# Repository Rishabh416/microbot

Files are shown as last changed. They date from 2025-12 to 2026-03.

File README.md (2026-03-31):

# Microbot

My first fully custom project inspired by the microbots from the movie Big Hero 6. My goal is to get into swarm robotics and I believe this is a HUGE leap in that direction, but a good moment to learn. I made this project to learn about swarm robotics and the potential application in environmental applications such as in deserts. 

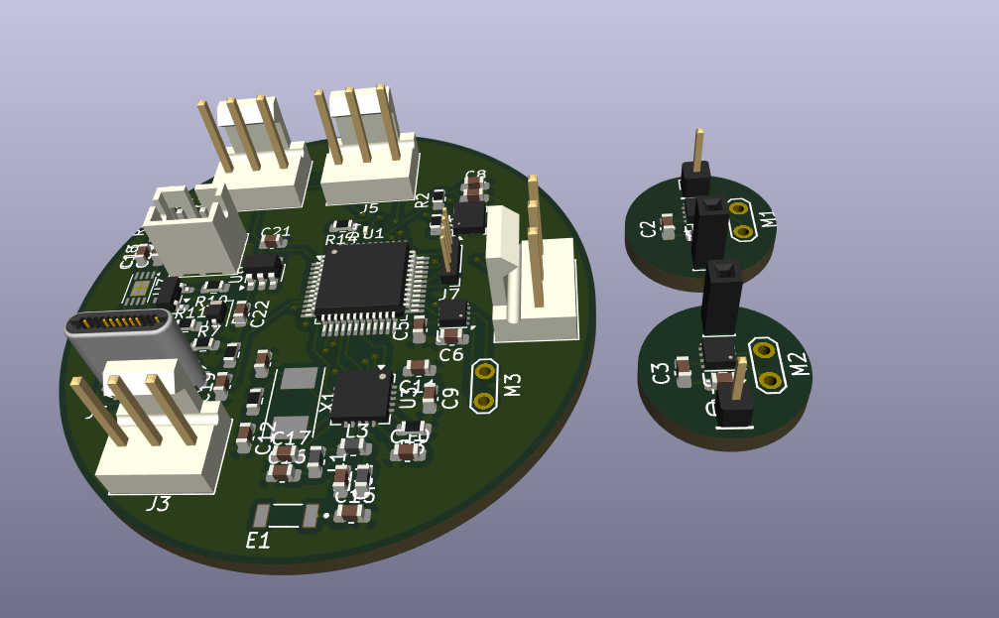
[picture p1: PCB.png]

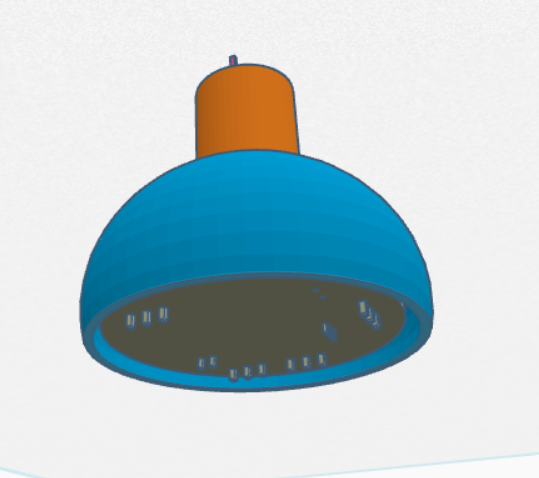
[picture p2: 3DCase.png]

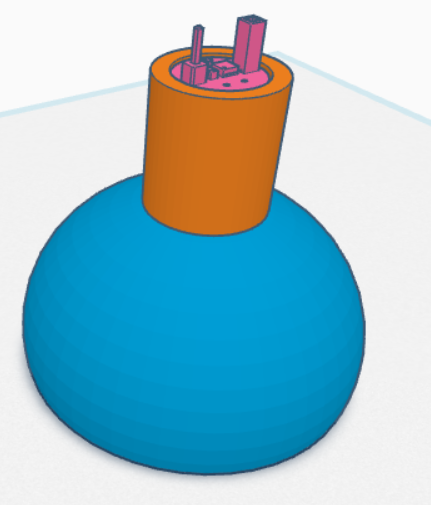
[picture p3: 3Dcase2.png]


| Part Number | JLC Part Number | Description | Manufacturer | Package | URL |
| :--- | :--- | :--- | :--- | :--- | :--- |
| STM32F103C8T6 | C8734 | STM32 MCU | STMicroelectronics | LQFP-48(7x7) | [Link](https://jlcpcb.com/partdetail/STMicroelectronics-STM32F103C8T6/C8734) |
| N/A | N/A | Electromagnet | | | |
| | N/A | Servo Motor | | | |
| | N/A | DC Motor | | | |
| ICM-42688-P(TOKMAS) | C54308212 | IMU | Tokmas | LGA-14(2.5x3) | [Link](https://jlcpcb.com/partdetail/Tokmas-ICM_42688_P_TOKMAS/C54308212) |
| NRF24L01P-R | C8791 | NRF24 | Nordic Semicon | QFN-20-EP(4x4) | [Link](https://jlcpcb.com/partdetail/NordicSemicon-NRF24L01PR/C8791) |
| KH-204065-DZ | C530676 | Pogo Male | Shenzhen Kinghelm Elec | SMD, D=2mm | [Link](https://jlcpcb.com/partdetail/Shenzhen_KinghelmElec-KH_204065DZ/C530676) |
| BWCD-L4.5W2.0H2.3 | C2826546 | Pogo Female | BAT WIRELESS | SMD, D=2mm | [Link](https://jlcpcb.com/partdetail/BATWIRELESS-BWCD_L4_5W2_0H23/C2826546) |
| | N/A | LiPo Battery | | | |
| MCP73831-2ATI/MC | C635036 | BMS | Microchip Tech | DFN-8-EP(2x3) | [Link](https://jlcpcb.com/partdetail/MicrochipTech-MCP73831_2ATIMC/C635036) |
| XC6220B331MR-G | C86534 | Voltage Regulator | Torex Semicon | SOT-25 | [Link](https://jlcpcb.com/partdetail/TorexSemicon-XC6220B331MRG/C86534) |
| DRV8837CDSGR | C191000 | Motor Driver | Texas Instruments | WSON-8-EP(2x2) | [Link](https://jlcpcb.com/partdetail/TexasInstruments-DRV8837CDSGR/C191000) |
| 2450AT18A100E | C89334 | Antenna | Johanson Dielectrics | 1206 | [Link](https://jlcpcb.com/partdetail/JohansonDielectrics-2450AT18A100E/C89334) |
| 16M 12PF 10PPM | C2975359 | 16MHz Crystal | SST | HC-49S-SMD-2P-Mini | [Link](https://jlcpcb.com/partdetail/SST-16M_12PF10PPM/C2975359) |
| SSM3J338R,LF | C146352 | MOSFET | TOSHIBA | SOT-23F | [Link](https://jlcpcb.com/partdetail/TOSHIBA-SSM3J338RLF/C146352) |
| | | Capacitors | | 0603 | |
| HVRTB-3433EPX | C5246356 | Green LED | HONGLITRONIC | SMD-6P, 3.4x3.3mm | [Link](https://jlcpcb.com/partdetail/5956669-HVRTB3433EPX/C5246356) |
| | | Diodes | | D_SOD-323 | |
| TJ-S0704EX4T5ALC2R-A5 | C48689442 | Red LED | TOGIALED | 0201 | [Link](https://jlcpcb.com/partdetail/TOGIALED-TJ_S0704EX4T5ALC2RA5/C48689442) |
| 918-118A2021Y40002 | C399939 | USB C | Jing Extension | SMD | [Link](https://jlcpcb.com/partdetail/383027-918118A2021Y40002/C399939) |
| B2B-PH-K-S-GW | C5251182 | Conn_01x02 | JST | 插件, P=2mm | [Link](https://jlcpcb.com/partdetail/JST-B2B_PH_K_SGW/C5251182) |
| 2.54-1*3P针 | C49257 | Conn_01x03_Pin | BOOMELE | 插件, P=2.54mm | [Link](https://jlcpcb.com/partdetail/50265-2_54_1_3P/C49257) |
| 2.54-1*4 | C5116483 | Conn_01x04_Pin | ZHOURI | 插件, P=2.54mm | [Link](https://jlcpcb.com/partdetail/ZHOURI-2_54_14/C5116483) |
| | | Inductors | | 0603 | |
| | | Resistors | | 0603 | |

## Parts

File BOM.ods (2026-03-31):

Part Number | JLC Part Number | Description | Manufacturer | Package | URL
STM32F103C8T6 | C8734 | STM32 MCU | STMicroelectronics | LQFP-48(7x7) | https://jlcpcb.com/partdetail/STMicroelectronics-STM32F103C8T6/C8734
N/A | N/A | Electromagnet
 | N/A | Servo Motor
 | N/A | DC Motor
ICM-42688-P(TOKMAS) | C54308212 | IMU | Tokmas | LGA-14(2.5x3) | https://jlcpcb.com/partdetail/Tokmas-ICM_42688_P_TOKMAS/C54308212
NRF24L01P-R | C8791 | NRF24 | Nordic Semicon | QFN-20-EP(4x4) | https://jlcpcb.com/partdetail/NordicSemicon-NRF24L01PR/C8791
KH-204065-DZ | C530676 | Pogo Male | Shenzhen Kinghelm Elec | SMD,D=2mm | https://jlcpcb.com/partdetail/Shenzhen_KinghelmElec-KH_204065DZ/C530676
BWCD-L4.5W2.0H2.3 | C2826546 | Pogo Female | BAT WIRELESS | SMD,D=2mm | https://jlcpcb.com/partdetail/BATWIRELESS-BWCD_L4_5W2_0H23/C2826546
 | N/A | LiPo Battery
MCP73831-2ATI/MC | C635036 | BMS | Microchip Tech | DFN-8-EP(2x3) | https://jlcpcb.com/partdetail/MicrochipTech-MCP73831_2ATIMC/C635036
XC6220B331MR-G | C86534 | Voltage Regulator | Torex Semicon | SOT-25 | https://jlcpcb.com/partdetail/TorexSemicon-XC6220B331MRG/C86534
DRV8837CDSGR | C191000 | Motor Driver | Texas Instruments | WSON-8-EP(2x2) | https://jlcpcb.com/partdetail/TexasInstruments-DRV8837CDSGR/C191000
2450AT18A100E | C89334 | Antenna | Johanson Dielectrics | 1206 | https://jlcpcb.com/partdetail/JohansonDielectrics-2450AT18A100E/C89334
16M 12PF 10PPM | C2975359 | 16MHz Crystal | SST | HC-49S-SMD-2P-Mini | https://jlcpcb.com/partdetail/SST-16M_12PF10PPM/C2975359
SSM3J338R,LF | C146352 | MOSFET | TOSHIBA | SOT-23F | https://jlcpcb.com/partdetail/TOSHIBA-SSM3J338RLF/C146352
 |  | Capacitors |  | 0603
HVRTB-3433EPX | C5246356 | Green LED | HONGLITRONIC(Hongli Zhihui (HONGLITRONIC)) | SMD-6P,3.4x3.3mm | https://jlcpcb.com/partdetail/5956669-HVRTB3433EPX/C5246356
 |  | Diodes |  | D_SOD-323
TJ-S0704EX4T5ALC2R-A5 | C48689442 | Red LED | TOGIALED | 0201 | https://jlcpcb.com/partdetail/TOGIALED-TJ_S0704EX4T5ALC2RA5/C48689442
918-118A2021Y40002 | C399939 | USB C | Jing Extension of the Electronic Co. | SMD | https://jlcpcb.com/partdetail/383027-918118A2021Y40002/C399939
B2B-PH-K-S-GW | C5251182 | Conn_01x02 | JST | 插件,P=2mm | https://jlcpcb.com/partdetail/JST-B2B_PH_K_SGW/C5251182
2.54-1*3P针 | C49257 | Conn_01x03_Pin | BOOMELE(Boom Precision Elec) | 插件,P=2.54mm | https://jlcpcb.com/partdetail/50265-2_54_1_3P/C49257
2.54-1*4 | C5116483 | Conn_01x04_Pin | ZHOURI | 插件,P=2.54mm | https://jlcpcb.com/partdetail/ZHOURI-2_54_14/C5116483
 |  | Inductors |  | 0603
 |  | Resistors |  | 0603

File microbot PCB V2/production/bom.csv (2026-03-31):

Designator | Footprint | Quantity | Value | LCSC Part #
C1, C2, C3, C4, C5, C6, C7, C8 | 0603 | 8 | 100n
C10, C19 | 0603 | 2 | 1n
C11 | 0603 | 1 | 33n
C12, C13 | 0603 | 2 | 22p
C14 | 0603 | 1 | 1.5p
C15 | 0603 | 1 | 1p
C16 | 0603 | 1 | 2.2n
C17 | 0603 | 1 | 4.7p
C18, C21 | 0603 | 2 | 10u
C20 | 0603 | 1 | 4.7u
C22 | 0603 | 1 | 1u
C9 | 0603 | 1 | 10n
D1 | 0201 | 1 | Green
D2, D3 | D_SOD-323 | 2 | 1N5819WS
D4 | 0201 | 1 | Red
E1 | XCVR_2450AT18A0100001E | 1 | 2450AT18A0100001E
J1 | USB_C_Plug_ShenzhenJingTuoJin_918-118A2021Y40002_Vertical | 1 | USB_C_Receptacle_PowerOnly_6P
J2 | JST_PH_B2B-PH-K_1x02_P2.00mm_Vertical | 1 | Conn_01x02
J3, J4, J5, J6 | FanPinHeader_1x03_P2.54mm_Vertical | 4 | Conn_01x03_Pin
J7 | PinHeader_1x04_P1.00mm_Vertical | 1 | Conn_01x04_Pin
L1 | 0603 | 1 | 2.7n
L2 | 0603 | 1 | 3.9n
L3 | 0603 | 1 | 8.2n
M1, M2, M3 | TestPoint_2Pads_Pitch2.54mm_Drill0.8mm | 3 | Motor_DC
Q1 | SOT-23 | 1 | Si2371EDS
R1, R10, R11, R2, R5, R6 | 0603 | 6 | 10k
R12 | 0603 | 1 | 75k
R13 | 0603 | 1 | 100k
R14 | 0603 | 1 | 150
R3 | 0603 | 1 | 22k
R4, R9 | 0603 | 2 | 1M
R7, R8 | 0603 | 2 | 5.1k
TP1, TP3 | PinHeader_1x01_P2.00mm_Vertical | 2 | MalePogo
TP2, TP4 | PinSocket_1x01_P2.00mm_Vertical | 2 | FemalePogo
U1 | LQFP-48_7x7mm_P0.5mm | 1 | STM32F103C8Tx
U2 | LGA-14_3x2.5mm_P0.5mm_LayoutBorder3x4y | 1 | LSM6DS3
U3 | QFN-20-1EP_4x4mm_P0.5mm_EP2.5x2.5mm | 1 | nRF24L01P
U4, U5, U6 | WSON-8-1EP_2x2mm_P0.5mm_EP0.9x1.6mm | 3 | DRV8837C
U7 | DFN-8-1EP_3x2mm_P0.5mm_EP1.7x1.4mm | 1 | MCP73831-2-MC
U8 | SOT-23-5 | 1 | XC6220B331MR
X1 | Crystal_SMD_Abracon_ABM7-2Pin_6.0x3.5mm | 1 | 16MHz

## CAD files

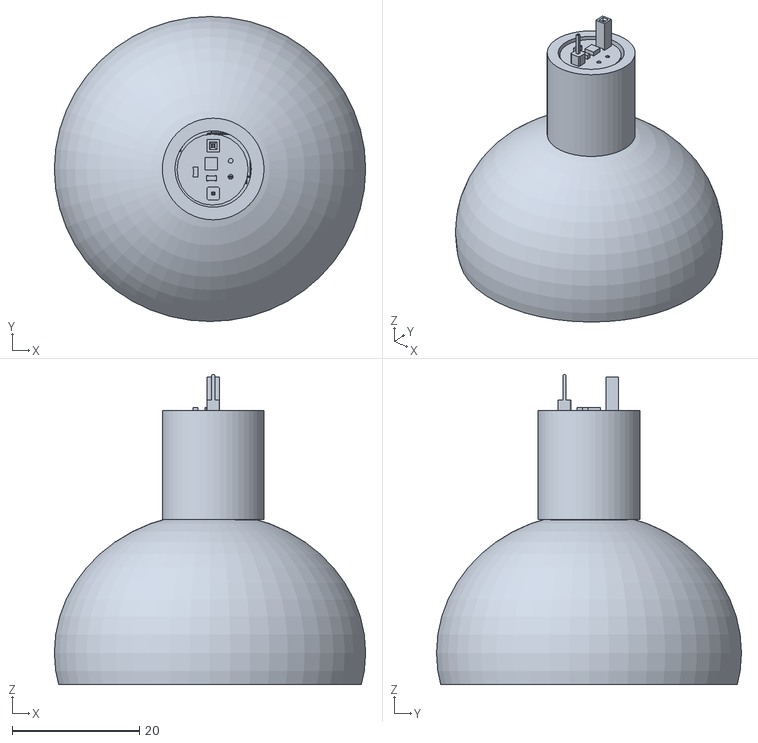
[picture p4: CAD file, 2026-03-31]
Microbot Case V2.stl
49.0 x 48.0 x 48.8

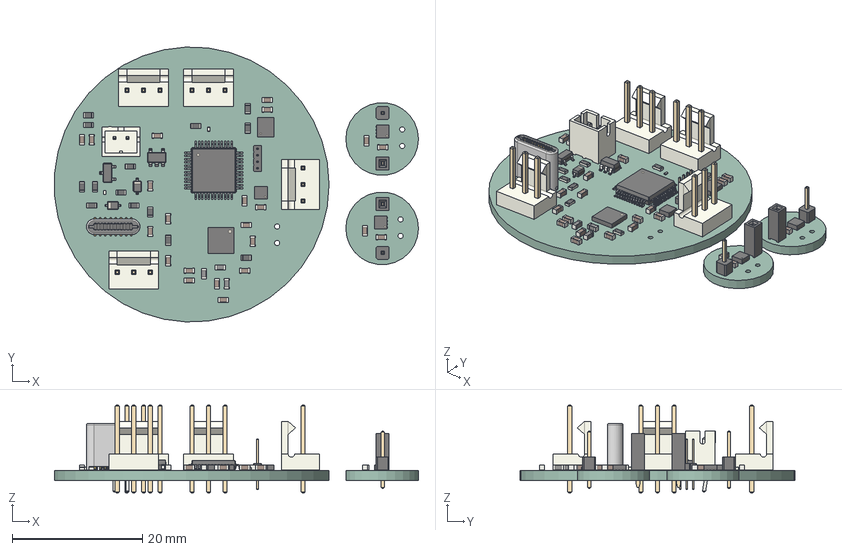
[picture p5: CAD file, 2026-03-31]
microbot PCB V2/MicroBot.step
56.0 x 42.3 x 13.5 mm
JST_PH_B2B-PH-K_1x02_P2.00mm_Vertical
C_0603_1608Metric x 22
R_0603_1608Metric x 14
USB_C_Plug_ShenzhenJingTuoJin_918-118A2021Y40002_Vertical
D_SOD-323 x 2
PinSocket_1x01_P2.00mm_Vertical x 2
PinHeader_1x01_P2.00mm_Vertical x 2
LED_0201_0603Metric x 2
L_0603_1608Metric x 3
SOT-23-5
FanPinHeader_1x03_P2.54mm_Vertical x 4
QFN-20-1EP_4x4mm_P0.5mm_EP2.5x2.5mm
WSON-8-1EP_2x2mm_P0.5mm_EP0.9x1.6mm x 3
LQFP-48_7x7mm_P0.5mm
LGA-14_3x2.5mm_P0.5mm_LayoutBorder3x4y
SOT-23
PinHeader_1x04_P1.00mm_Vertical
MicroBot_PCB_1
MicroBot_PCB_2
MicroBot_PCB_3

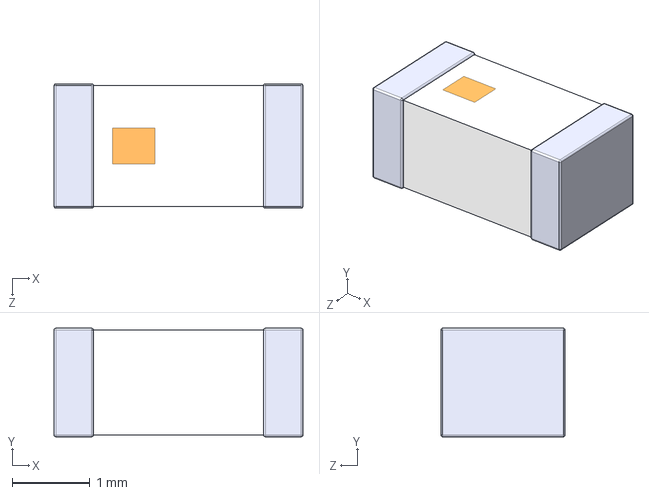
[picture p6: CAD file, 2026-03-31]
microbot PCB V2/SymbolFootprint/2450AT18A0100001E/2450AT18A0100001E.step
3.20 x 1.40 x 1.60 mm

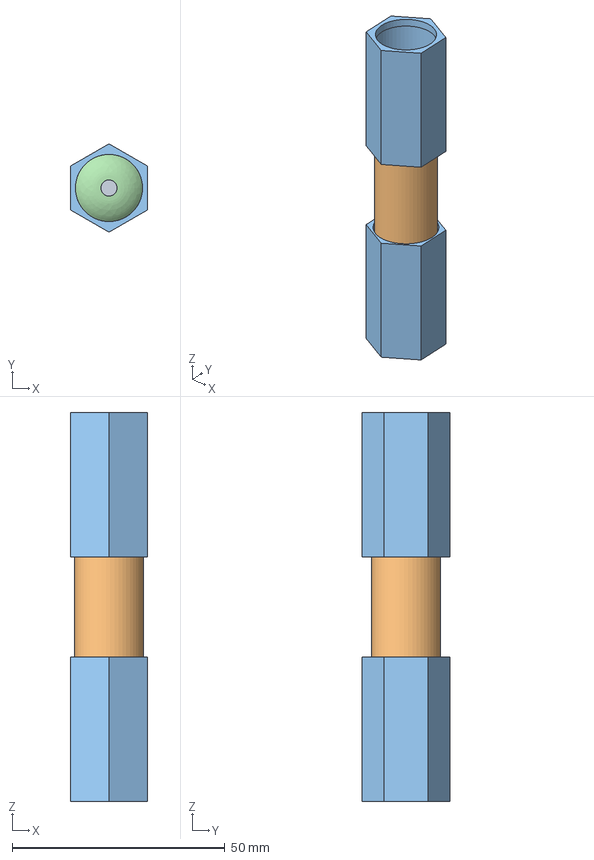
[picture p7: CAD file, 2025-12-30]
Microbot Case.step
18.0 x 20.8 x 91.5 mm
PCB
Central Case
Arm

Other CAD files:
Microbot Case.f3d
Microbot.f3d

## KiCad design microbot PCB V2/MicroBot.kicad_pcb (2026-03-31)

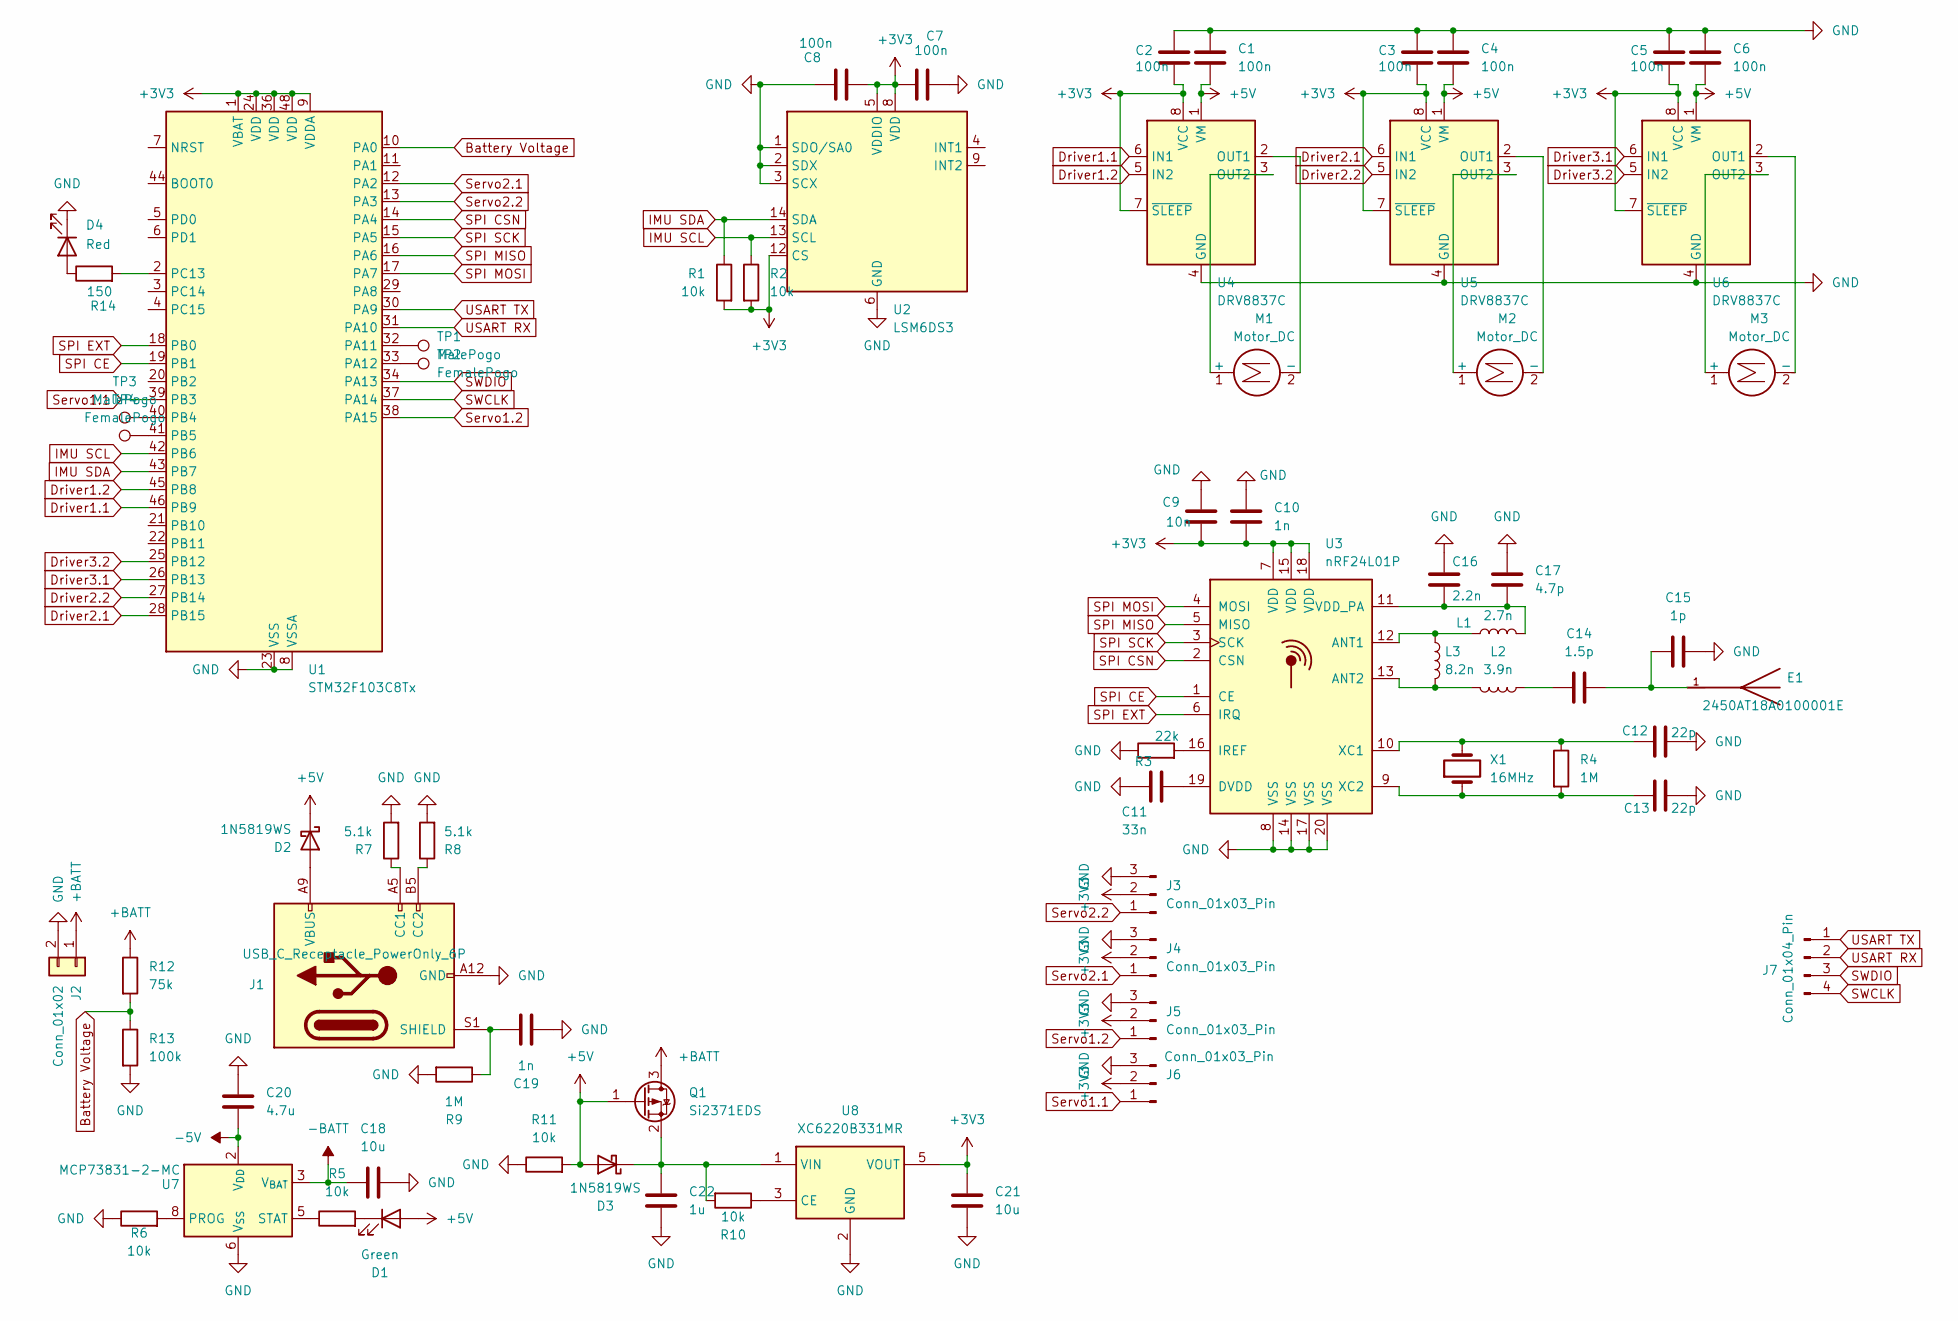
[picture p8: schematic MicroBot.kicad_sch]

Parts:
C1, C2, C3, C4, C5, C6, C7, C8: 100n; C_0603_1608Metric
C9: 10n; C_0603_1608Metric
C10, C19: 1n; C_0603_1608Metric
C11: 33n; C_0603_1608Metric
C12, C13: 22p; C_0603_1608Metric
C14: 1.5p; C_0603_1608Metric
C15: 1p; C_0603_1608Metric
C16: 2.2n; C_0603_1608Metric
C17: 4.7p; C_0603_1608Metric
C18, C21: 10u; C_0603_1608Metric
C20: 4.7u; C_0603_1608Metric
C22: 1u; C_0603_1608Metric
D1: Green; LED_0201_0603Metric
D2, D3: 1N5819WS; D_SOD-323
D4: Red; LED_0201_0603Metric
E1: 2450AT18A0100001E; XCVR_2450AT18A0100001E; PARTREV 4.0
J1: USB_C_Receptacle_PowerOnly_6P; USB_C_Plug_ShenzhenJingTuoJin_918-118A2021Y40002_Vertical
J2: Conn_01x02; JST_PH_B2B-PH-K_1x02_P2.00mm_Vertical
J3, J4, J5, J6: Conn_01x03_Pin; FanPinHeader_1x03_P2.54mm_Vertical
J7: Conn_01x04_Pin; PinHeader_1x04_P1.00mm_Vertical
L1: 2.7n; L_0603_1608Metric
L2: 3.9n; L_0603_1608Metric
L3: 8.2n; L_0603_1608Metric
M1, M2, M3: Motor_DC; TestPoint_2Pads_Pitch2.54mm_Drill0.8mm
Q1: Si2371EDS; SOT-23
R1, R2, R5, R6, R10, R11: 10k; R_0603_1608Metric
R3: 22k; R_0603_1608Metric
R4, R9: 1M; R_0603_1608Metric
R7, R8: 5.1k; R_0603_1608Metric
R12: 75k; R_0603_1608Metric
R13: 100k; R_0603_1608Metric
R14: 150; R_0603_1608Metric
TP1, TP3: MalePogo; PinHeader_1x01_P2.00mm_Vertical
TP2, TP4: FemalePogo; PinSocket_1x01_P2.00mm_Vertical
U1: STM32F103C8Tx; LQFP-48_7x7mm_P0.5mm
U2: LSM6DS3; LGA-14_3x2.5mm_P0.5mm_LayoutBorder3x4y
U3: nRF24L01P; QFN-20-1EP_4x4mm_P0.5mm_EP2.5x2.5mm
U4, U5, U6: DRV8837C; WSON-8-1EP_2x2mm_P0.5mm_EP0.9x1.6mm
U7: MCP73831-2-MC; DFN-8-1EP_3x2mm_P0.5mm_EP1.7x1.4mm
U8: XC6220B331MR; SOT-23-5
X1: 16MHz; Crystal_SMD_Abracon_ABM7-2Pin_6.0x3.5mm

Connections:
+3V3: C2.2, C3.2, C5.2, C7.1, C8.1, C9.1, C10.2, C21.1, J3.2, J4.2, J5.2, J6.2, R1.2, R2.2, U1.1 (VBAT), U1.9 (VDDA), U1.24 (VDD), U1.36 (VDD), U1.48 (VDD), U2.5 (VDDIO), U2.8 (VDD), U2.12 (CS), U3.7 (VDD), U3.15 (VDD), U3.18 (VDD), U4.7 (~SLEEP), U4.8 (VCC), U5.7 (~SLEEP), U5.8 (VCC), U6.7 (~SLEEP), U6.8 (VCC), U8.5 (VOUT)
+5V: C1.1, C4.1, C6.1, D1.2 (A), D2.1 (K), D3.2 (A), Q1.1 (G), R11.2, U4.1 (VM), U5.1 (VM), U6.1 (VM)
+BATT: J2.1, Q1.3 (D), R12.1
-5V: C20.1, U7.1 (V_{DD}), U7.2 (V_{DD})
-BATT: C18.1, U7.3 (V_{BAT}), U7.4 (V_{BAT})
Battery Voltage: R12.2, R13.1, U1.10 (PA0)
Driver1.1: U1.46 (PB9), U4.6 (IN1)
Driver1.2: U1.45 (PB8), U4.5 (IN2)
Driver2.1: U1.28 (PB15), U5.6 (IN1)
Driver2.2: U1.27 (PB14), U5.5 (IN2)
Driver3.1: U1.26 (PB13), U6.6 (IN1)
Driver3.2: U1.25 (PB12), U6.5 (IN2)
GND: C1.2, C2.1, C3.1, C4.2, C5.1, C6.2, C7.2, C8.2, C9.2, C10.1, C11.1, C12.2, C13.2, C15.2, C16.1, C17.1, C18.2, C19.1, C20.2, C21.2, C22.2, D4.1 (K), J1.A12 (GND), J1.B12 (GND), J2.2, J3.3, J4.3, J5.3, J6.3, R3.1, R6.1, R7.2, R8.2, R9.2, R11.1, R13.2, U1.8 (VSSA), U1.23 (VSS), U1.35 (VSS), U1.47 (VSS), U2.1 (SDO/SA0), U2.2 (SDX), U2.3 (SCX), U2.6 (GND), U2.7 (GND), U3.8 (VSS), U3.14 (VSS), U3.17 (VSS), U3.20 (VSS), U4.4 (GND), U4.9 (GND), U5.4 (GND), U5.9 (GND), U6.4 (GND), U6.9 (GND), U7.6 (V_{SS}), U8.2 (GND)
IMU SCL: R2.1, U1.42 (PB6), U2.13 (SCL)
IMU SDA: R1.1, U1.43 (PB7), U2.14 (SDA)
unnamed: C14.1, L2.1
unnamed: C14.2, C15.1, E1.1
unnamed: D1.1 (K), R5.2
unnamed: D2.2 (A), J1.A9 (VBUS), J1.B9 (VBUS)
unnamed: C22.1, D3.1 (K), Q1.2 (S), R10.2, U8.1 (VIN)
unnamed: D4.2 (A), R14.1
unnamed: J1.A5 (CC1), R7.1
unnamed: J1.B5 (CC2), R8.1
unnamed: C19.2, J1.S1 (SHIELD), R9.1
unnamed: M1.1 (+), U4.3 (OUT2)
unnamed: M1.2 (-), U4.2 (OUT1)
unnamed: M2.1 (+), U5.3 (OUT2)
unnamed: M2.2 (-), U5.2 (OUT1)
unnamed: M3.1 (+), U6.3 (OUT2)
unnamed: M3.2 (-), U6.2 (OUT1)
unnamed: TP1.1, U1.32 (PA11)
unnamed: TP2.1, U1.33 (PA12)
unnamed: TP3.1, U1.40 (PB4)
unnamed: TP4.1, U1.41 (PB5)
unnamed: R14.2, U1.2 (PC13)
unnamed: L1.1, L3.1, U3.12 (ANT1)
unnamed: L2.2, L3.2, U3.13 (ANT2)
unnamed: C11.2, U3.19 (DVDD)
unnamed: R3.2, U3.16 (IREF)
unnamed: C16.2, C17.2, L1.2, U3.11 (VDD_PA)
unnamed: C12.1, R4.1, U3.10 (XC1), X1.2
unnamed: C13.1, R4.2, U3.9 (XC2), X1.1
unnamed: R6.2, U7.8 (PROG)
unnamed: R5.1, U7.5 (STAT)
unnamed: R10.1, U8.3 (CE)
SPI CE: U1.19 (PB1), U3.1 (CE)
SPI CSN: U1.14 (PA4), U3.2 (CSN)
SPI EXT: U1.18 (PB0), U3.6 (IRQ)
SPI MISO: U1.16 (PA6), U3.5 (MISO)
SPI MOSI: U1.17 (PA7), U3.4 (MOSI)
SPI SCK: U1.15 (PA5), U3.3 (SCK)
SWCLK: J7.4, U1.37 (PA14)
SWDIO: J7.3, U1.34 (PA13)
Servo1.1: J6.1, U1.39 (PB3)
Servo1.2: J5.1, U1.38 (PA15)
Servo2.1: J4.1, U1.12 (PA2)
Servo2.2: J3.1, U1.13 (PA3)
USART RX: J7.2, U1.31 (PA10)
USART TX: J7.1, U1.30 (PA9)

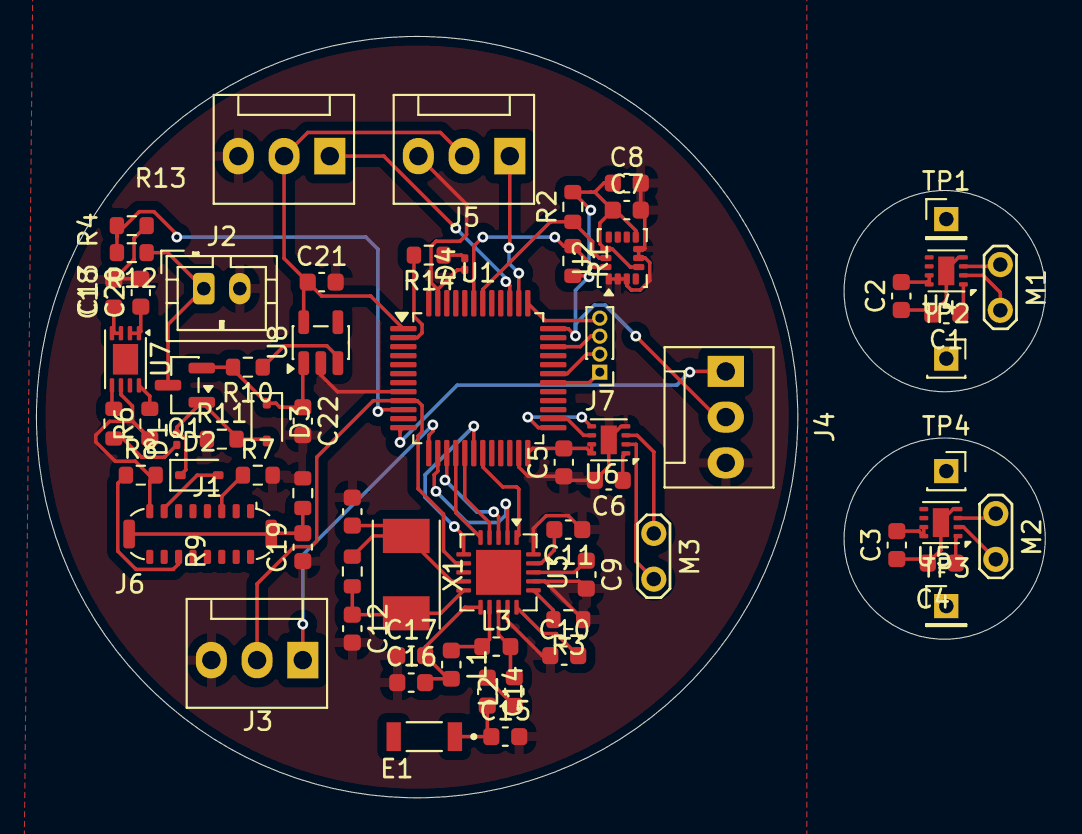
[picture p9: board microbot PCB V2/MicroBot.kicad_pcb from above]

Board: 2 copper layers, 42.3 x 42.3 mm, 68 parts (0 on the bottom side), 59 nets.

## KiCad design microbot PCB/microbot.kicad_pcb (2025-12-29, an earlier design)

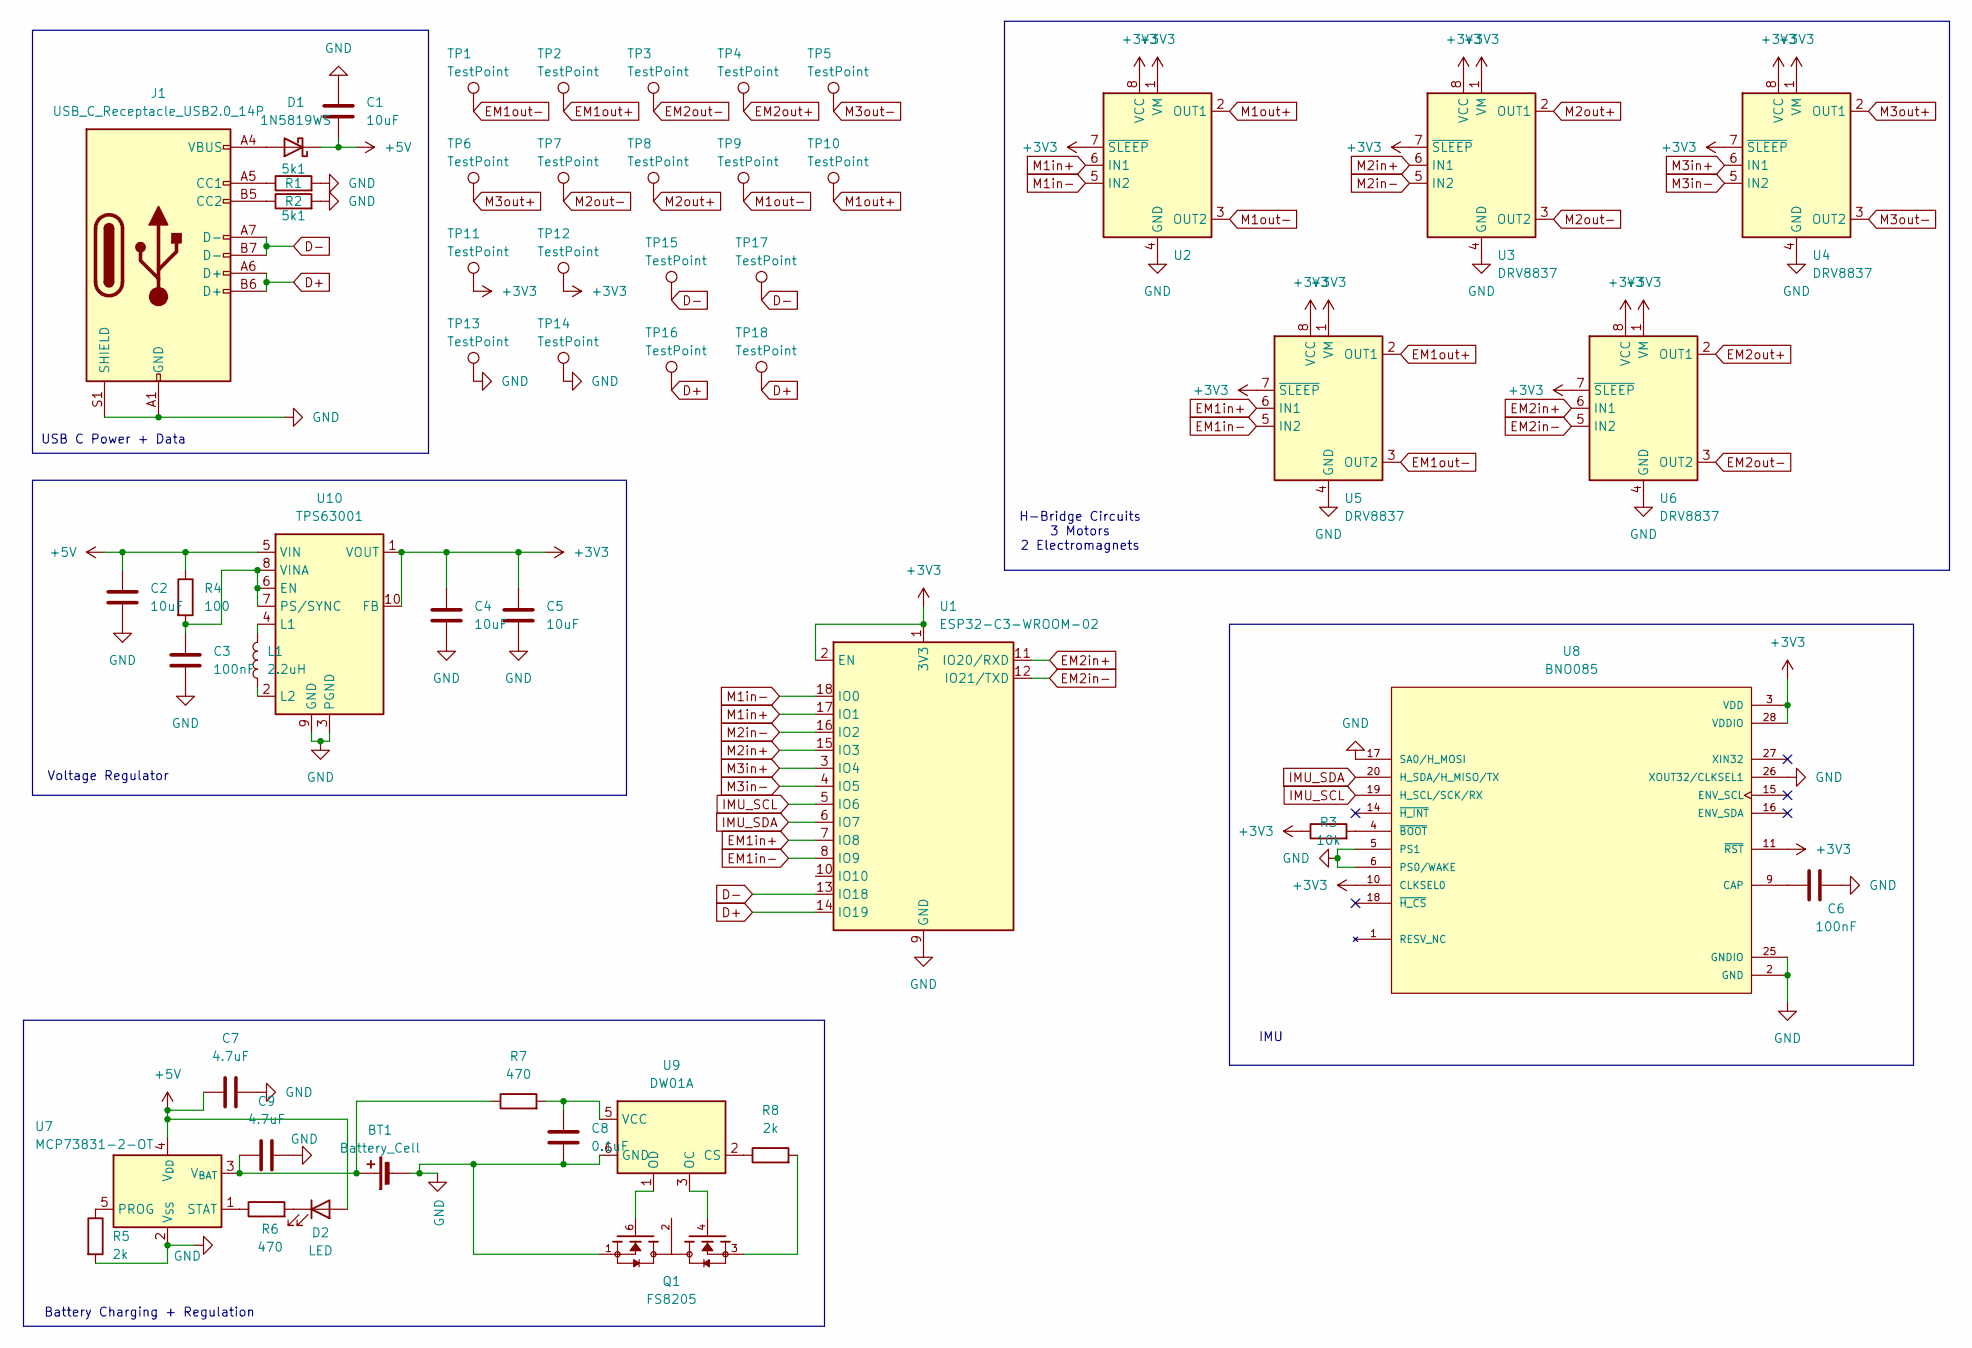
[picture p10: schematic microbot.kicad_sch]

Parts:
BT1: Battery_Cell; JST_EH_S2B-EH_1x02_P2.50mm_Horizontal
C1, C2, C4, C5: 10uF; C_0603_1608Metric
C3, C6: 100nF; C_0603_1608Metric
C7, C9: 4.7uF; C_0603_1608Metric
C8: 0.1uF; C_0603_1608Metric
D1: 1N5819WS; D_SOD-323
D2: LED; LED_0603_1608Metric
J1: USB_C_Receptacle_USB2.0_14P; USB_C_Receptacle_G-Switch_GT-USB-7051x
L1: 2.2uH; L_0603_1608Metric
Q1: FS8205; SOT95P280X145-6N; PARTREV 1.9
R1, R2: 5k1; R_0603_1608Metric
R3: 10k; R_0603_1608Metric
R4: 100; R_0603_1608Metric
R5, R8: 2k; R_0603_1608Metric
R6, R7: 470; R_0603_1608Metric
TP1, TP2, TP3, TP4, TP5, TP6, TP7, TP8, TP9, TP10, TP11, TP12, TP13, TP14, TP15, TP16, TP17, TP18: TestPoint; TestPoint_Pad_1.0x1.0mm
U1: ESP32-C3-WROOM-02
U2, U3, U4, U5, U6: DRV8837; WSON-8-1EP_2x2mm_P0.5mm_EP0.9x1.6mm
U7: MCP73831-2-OT; SOT-23-5
U8: BNO085; IC_BNO085; PARTREV v1.17
U9: DW01A; SOT-23-6
U10: TPS63001; Texas_DRC0010J_ThermalVias

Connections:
+3V3: C4.1, C5.1, R3.1, TP11.1, TP12.1, U1.1 (3V3), U1.2 (EN), U2.1 (VM), U2.7 (~SLEEP), U2.8 (VCC), U3.1 (VM), U3.7 (~SLEEP), U3.8 (VCC), U4.1 (VM), U4.7 (~SLEEP), U4.8 (VCC), U5.1 (VM), U5.7 (~SLEEP), U5.8 (VCC), U6.1 (VM), U6.7 (~SLEEP), U6.8 (VCC), U8.3 (VDD), U8.10 (CLKSEL0), U8.11 (~RST), U8.28 (VDDIO), U10.1 (VOUT), U10.10 (FB)
+5V: C1.2, C2.1, C7.1, D1.1 (K), D2.2 (A), R4.1, U7.4 (V_{DD}), U10.5 (VIN)
D+: J1.A6 (D+), J1.B6 (D+), TP16.1, TP18.1, U1.14 (IO19)
D-: J1.A7 (D-), J1.B7 (D-), TP15.1, TP17.1, U1.13 (IO18)
EM1in+: U1.7 (IO8), U5.6 (IN1)
EM1in-: U1.8 (IO9), U5.5 (IN2)
EM1out+: TP2.1, U5.2 (OUT1)
EM1out-: TP1.1, U5.3 (OUT2)
EM2in+: U1.11 (IO20/RXD), U6.6 (IN1)
EM2in-: U1.12 (IO21/TXD), U6.5 (IN2)
EM2out+: TP4.1, U6.2 (OUT1)
EM2out-: TP3.1, U6.3 (OUT2)
GND: BT1.2 (-), C1.1, C2.2, C3.2, C4.2, C5.2, C6.1, C7.2, C8.1, C9.2, J1.A1 (GND), J1.A12 (GND), J1.B1 (GND), J1.B12 (GND), J1.S1 (SHIELD), Q1.1, R1.2, R2.2, R5.2, TP13.1, TP14.1, U1.9 (GND), U1.19 (GND), U2.4 (GND), U2.9 (GND), U3.4 (GND), U3.9 (GND), U4.4 (GND), U4.9 (GND), U5.4 (GND), U5.9 (GND), U6.4 (GND), U6.9 (GND), U7.2 (V_{SS}), U8.2 (GND), U8.5 (PS1), U8.6 (PS0/WAKE), U8.17 (SA0/H_MOSI), U8.25 (GNDIO), U8.26 (XOUT32/CLKSEL1), U9.6 (GND), U10.3 (PGND), U10.9 (GND), U10.11 (PGND)
IMU_SCL: U1.5 (IO6), U8.19 (H_SCL/SCK/RX)
IMU_SDA: U1.6 (IO7), U8.20 (H_SDA/H_MISO/TX)
M1in+: U1.17 (IO1), U2.6 (IN1)
M1in-: U1.18 (IO0), U2.5 (IN2)
M1out+: TP10.1, U2.2 (OUT1)
M1out-: TP9.1, U2.3 (OUT2)
M2in+: U1.15 (IO3), U3.6 (IN1)
M2in-: U1.16 (IO2), U3.5 (IN2)
M2out+: TP8.1, U3.2 (OUT1)
M2out-: TP7.1, U3.3 (OUT2)
M3in+: U1.3 (IO4), U4.6 (IN1)
M3in-: U1.4 (IO5), U4.5 (IN2)
M3out+: TP6.1, U4.2 (OUT1)
M3out-: TP5.1, U4.3 (OUT2)
unnamed: BT1.1 (+), C9.1, R7.1, U7.3 (V_{BAT})
unnamed: D1.2 (A), J1.A4 (VBUS), J1.A9 (VBUS), J1.B4 (VBUS), J1.B9 (VBUS)
unnamed: D2.1 (K), R6.2
unnamed: J1.A5 (CC1), R1.1
unnamed: J1.B5 (CC2), R2.1
unnamed: Q1.2, Q1.5
unnamed: Q1.3, R8.2
unnamed: R5.1, U7.5 (PROG)
unnamed: R6.1, U7.1 (STAT)
unnamed: C6.2, U8.9 (CAP)
unnamed: R3.2, U8.4 (~BOOT)
unnamed: R8.1, U9.2 (CS)
unnamed: Q1.4, U9.3 (OC)
unnamed: Q1.6, U9.1 (OD)
unnamed: C8.2, R7.2, U9.5 (VCC)
unnamed: C3.1, R4.2, U10.6 (EN), U10.7 (PS/SYNC), U10.8 (VINA)
unnamed: L1.2, U10.4 (L1)
unnamed: L1.1, U10.2 (L2)

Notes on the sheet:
Battery Charging + Regulation
IMU
H-Bridge Circuits 3 Motors 2 Electromagnets
Voltage Regulator
USB C Power + Data

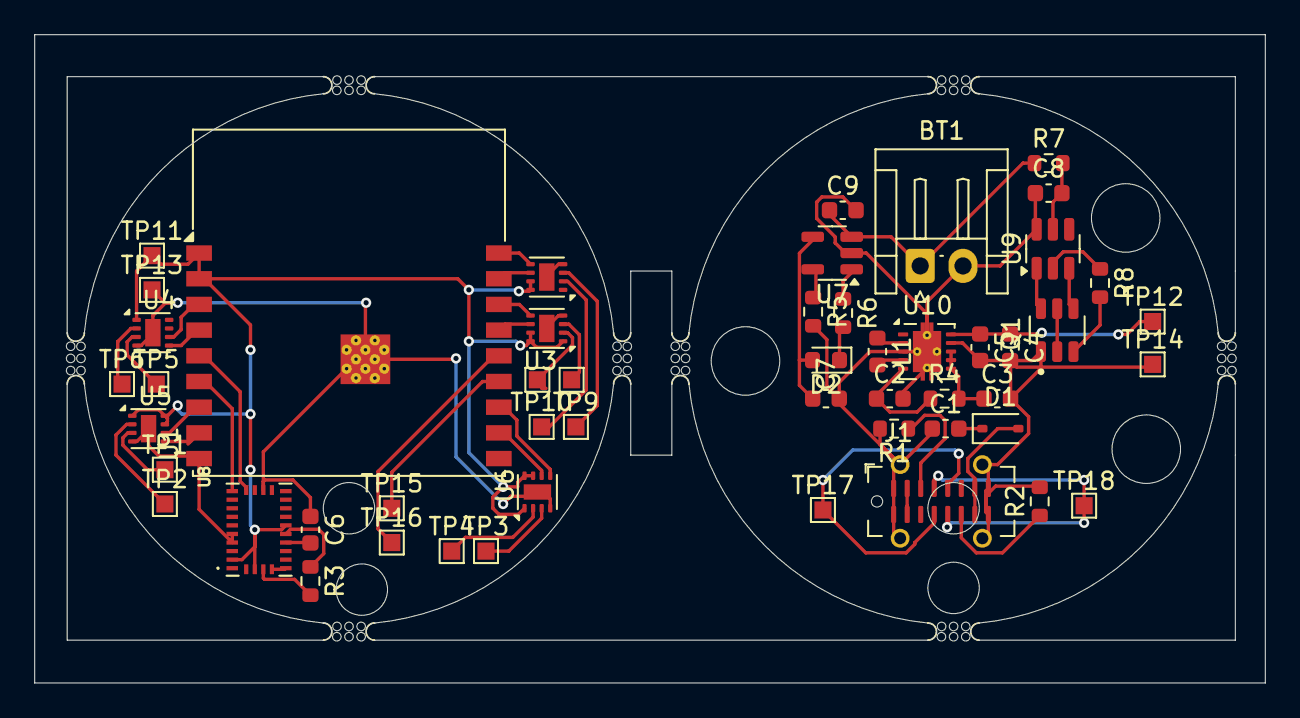
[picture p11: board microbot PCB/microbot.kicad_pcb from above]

Board: 2 copper layers, 71.8 x 37.9 mm, 59 parts (0 on the bottom side), 45 nets.

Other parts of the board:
mouse-bite-1mm-3mm, mouse-bite-1mm-3mm#2, mouse-bite-1mm-3mm#3, mouse-bite-1mm-3mm#4, mouse-bite-1mm-3mm#5, mouse-bite-1mm-3mm#6, mouse-bite-1mm-3mm#7, mouse-bite-1mm-3mm#8: VAL**; mouse-bite-1mm-3mm

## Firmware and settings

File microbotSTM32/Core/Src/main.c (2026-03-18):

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
/* Includes ------------------------------------------------------------------*/
#include "main.h"

/* USER CODE BEGIN Includes */
#include <stdint.h>
#include <string.h>
#include <stdio.h>
#include "NRF24.h"
#include "NRF24_reg_addresses.h"
#include "stm32f1xx_hal.h"
#include "stm32f1xx_hal_uart.h"
#include "ServoPair.h"
/* USER CODE END Includes */

/* USER CODE BEGIN PD */

#define PLD_SIZE 32
// #define tx

/* USER CODE END PD */

SPI_HandleTypeDef hspi1;

TIM_HandleTypeDef htim1;
TIM_HandleTypeDef htim2;

UART_HandleTypeDef huart1;

void SystemClock_Config(void);
static void MX_GPIO_Init(void);
static void MX_TIM2_Init(void);
static void MX_SPI1_Init(void);
static void MX_USART1_UART_Init(void);
static void MX_TIM1_Init(void);
/* USER CODE BEGIN 0 */
#ifdef tx
uint8_t data_T[PLD_SIZE] = {"hello"};
#else
uint8_t data_R[PLD_SIZE];
#endif

extern TIM_HandleTypeDef htim2;

ServoPair pair1;
ServoPair pair2;

/* USER CODE END 0 */

/**
  * @brief  The application entry point.
  * @retval int
  */
int main(void)
{

  /* MCU Configuration--------------------------------------------------------*/

  /* Reset of all peripherals, Initializes the Flash interface and the Systick. */
  HAL_Init();

  /* Configure the system clock */
  SystemClock_Config();

  /* Initialize all configured peripherals */
  MX_GPIO_Init();
  MX_TIM2_Init();
  MX_SPI1_Init();
  MX_USART1_UART_Init();
  MX_TIM1_Init();
  /* USER CODE BEGIN 2 */
  csn_high();
  nrf24_init();
  nrf24_tx_pwr(_0dbm);
  nrf24_data_rate(_1mbps);
  nrf24_set_channel(78);
  nrf24_pipe_pld_size(0, PLD_SIZE);
  nrf24_set_crc(en_crc, _1byte);
  uint8_t addr[5] = {0x10, 0x21, 0x32, 0x43, 0x54};
  nrf24_open_tx_pipe(addr);
  nrf24_open_rx_pipe(0, addr);

#ifdef tx
  nrf24_stop_listen();
#else
  nrf24_listen();
#endif

  HAL_TIM_PWM_Start(&htim2, TIM_CHANNEL_1);
  HAL_TIM_PWM_Start(&htim2, TIM_CHANNEL_2);
  HAL_TIM_PWM_Start(&htim2, TIM_CHANNEL_3);
  HAL_TIM_PWM_Start(&htim2, TIM_CHANNEL_4);

  ServoPair_init(&pair1, TIM_CHANNEL_1, TIM_CHANNEL_2);
  ServoPair_init(&pair2, TIM_CHANNEL_3, TIM_CHANNEL_4);
  /* USER CODE END 2 */

  /* Infinite loop */
  /* USER CODE BEGIN WHILE */
  while (1)
  {
    /* USER CODE END WHILE */

    /* USER CODE BEGIN 3 */
#ifdef tx
    nrf24_transmit(data_T, sizeof(data_T));
#else
    nrf24_listen();
    if(nrf24_data_available()) {
      nrf24_receive(data_R, sizeof(data_R));
    }

    char temp[40];
    sprintf(temp, "| %s |\r\n", data_R);
    HAL_UART_Transmit(&huart1, temp, strlen(temp), 100);

    for(uint8_t i=0; i<sizeof(data_R); i++) {
      data_R[i] = '\0';
    }
#endif

    HAL_GPIO_TogglePin(GPIOC, GPIO_PIN_13); // LED
    HAL_GPIO_TogglePin(GPIOB, GPIO_PIN_3); // electromagnet 1
    HAL_GPIO_TogglePin(GPIOB, GPIO_PIN_4); // electromagnet 2
    ServoPair_set(&pair1, 0, 25);
    ServoPair_set(&pair2, 50, 100);

    HAL_Delay(500);
  }
  /* USER CODE END 3 */
}

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


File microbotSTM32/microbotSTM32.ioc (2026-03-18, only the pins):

Mcu.UserName=STM32F103C8Tx
PA0-WKUP.GPIO_Label=servo0
PA0-WKUP.Signal=S_TIM2_CH1_ETR
PA1.GPIO_Label=servo1
PA1.Signal=S_TIM2_CH2
PA10.Signal=USART1_RX
PA2.GPIO_Label=servo2
PA2.Signal=S_TIM2_CH3
PA3.GPIO_Label=servo3
PA3.Signal=S_TIM2_CH4
PA5.Signal=SPI1_SCK
PA6.Signal=SPI1_MISO
PA7.Signal=SPI1_MOSI
PA9.Signal=USART1_TX
PB0.Signal=GPXTI0
PB1.GPIO_Label=CE
PB1.Signal=GPIO_Output
PB10.GPIO_Label=CSN
PB10.Signal=GPIO_Output
PB3.Signal=GPIO_Output
PB4.Signal=GPIO_Output
PC13-TAMPER-RTC.Signal=GPIO_Output

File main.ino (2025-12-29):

#include <Arduino.h>

const int m1pos = 0;  const int m1neg = 1;
const int m2pos = 2;  const int m2neg = 3;
const int m3pos = 4;  const int m3neg = 5;
const int em1pos = 8; const int em1neg = 9;
const int em2pos = 11; const int em2neg = 12;

void setup() {
  Serial.begin(115200);
  
  int pins[] = {m1pos, m1neg, m2pos, m2neg, m3pos, m3neg, em1pos, em1neg, em2pos, em2neg};
  for (int i = 0; i < 10; i++) {
    pinMode(pins[i], OUTPUT);
    digitalWrite(pins[i], LOW);
  }
}

void stopAll() {
  digitalWrite(m1pos, LOW); digitalWrite(m1neg, LOW);
  digitalWrite(m2pos, LOW); digitalWrite(m2neg, LOW);
  digitalWrite(m3pos, LOW); digitalWrite(m3neg, LOW);
  digitalWrite(em1pos, LOW); digitalWrite(em1neg, LOW);
  digitalWrite(em2pos, LOW); digitalWrite(em2neg, LOW);
}

void loop() {
  if (Serial.available() > 0) { 
    String command = Serial.readStringUntil('\n');
    command.trim(); 
    if (command == "stop") {
      stopAll();
      Serial.println("All motors stopped.");
      return;
    }

    int motor = command.substring(0, 1).toInt();
    char direction = command.charAt(command.length() - 1);
    int pwmValue = command.substring(1, command.length() - 1).toInt();

    int posPin, negPin;
    switch (motor) {
      case 1: posPin = m1pos; negPin = m1neg; break;
      case 2: posPin = m2pos; negPin = m2neg; break;
      case 3: posPin = m3pos; negPin = m3neg; break;
      case 4: posPin = em1pos; negPin = em1neg; break;
      case 5: posPin = em2pos; negPin = em2neg; break;
      default:
        Serial.println("Wrong motor");
        return;
    }

    if (direction == 'p') {
      analogWrite(negPin, 0);
      analogWrite(posPin, pwmValue); 
      Serial.printf("Motor %d Forward at %d\n", motor, pwmValue);
    } else if (direction == 'n') {
      analogWrite(posPin, 0);
      analogWrite(negPin, pwmValue);
      Serial.printf("Motor %d Reverse at %d\n", motor, pwmValue);
    } else {
      Serial.println("Invalid direction. Use 'p' or 'n'");
    }
  }
}

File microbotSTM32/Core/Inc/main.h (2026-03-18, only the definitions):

#define servo0_Pin GPIO_PIN_0
#define servo0_GPIO_Port GPIOA
#define servo1_Pin GPIO_PIN_1
#define servo1_GPIO_Port GPIOA
#define servo2_Pin GPIO_PIN_2
#define servo2_GPIO_Port GPIOA
#define servo3_Pin GPIO_PIN_3
#define servo3_GPIO_Port GPIOA
#define CE_Pin GPIO_PIN_1
#define CE_GPIO_Port GPIOB
#define CSN_Pin GPIO_PIN_10
#define CSN_GPIO_Port GPIOB

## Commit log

2025-12-30 added readme
    [Microbot Case.step, bom.csv]
2026-03-12 working LED blink
2026-03-13 working servo (needs calibration) and magnet
2026-03-31 Updated files for V2
    [2450AT18A0100001E.step, BOM.ods, MicroBot.kicad_pcb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]

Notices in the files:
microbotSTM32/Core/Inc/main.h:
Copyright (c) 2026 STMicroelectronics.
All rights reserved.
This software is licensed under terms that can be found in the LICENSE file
